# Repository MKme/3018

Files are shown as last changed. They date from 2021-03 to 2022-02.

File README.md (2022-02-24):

<p align="center">
<b>Adventures with the 3018 CNC Router </b><br>
<br><br>
<br>🐦 <a href="https://twitter.com/mkmeorg">Twitter</a>
| 📺 <a href="https://www.youtube.com/mkmeorg">YouTube</a>
| 🌍 <a href="http://www.mkme.org">mkme.org</a><br>
<br>
Support this project and become a patron on <a href="https://www.patreon.com/EricWilliam">Patreon</a>.<br>
Chat: <a href="https://discord.gg/j9S4Fgv">Discord</a></b>!
</p>

# 3018
I bought the 3018 CNC as a cheap DIY kit and built it live on YouTube at the links below.  This repo is where I am storing all the information, guides, tutorials, parts and supplies  use in this build.
I have linked the exact parts and supplies you will see in upcoming videos on the main channel. So far it seems to be a great kit.  I am totally new to CNC but have 3D Printing and laser cutting experience. 

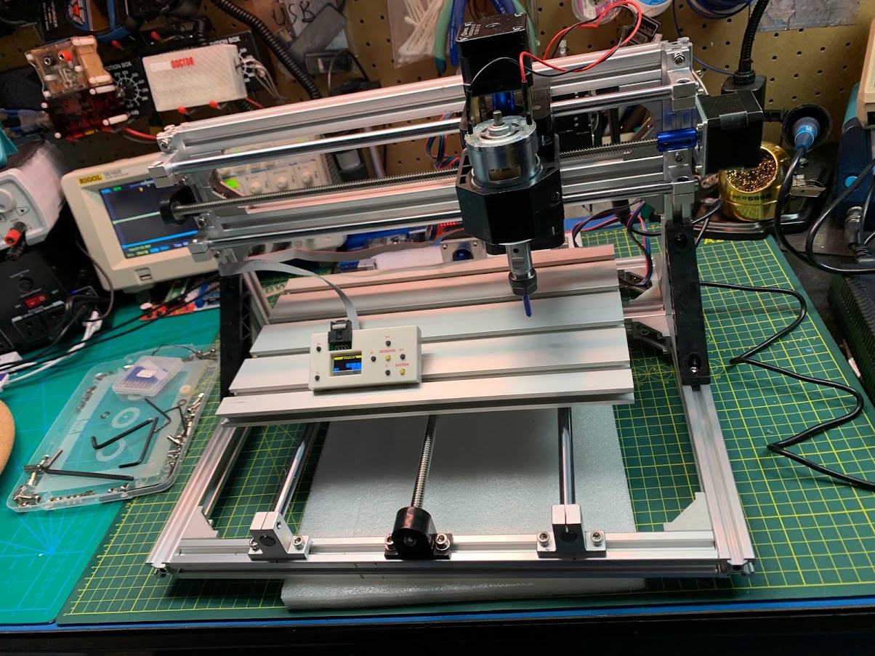
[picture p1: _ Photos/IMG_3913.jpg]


## Parts:

All the parts Ive used to build the 3018 and upgrades I have added 

| Component | Source  |
| --- |---|
| Amazon- 3018 CNC Machine | https://amzn.to/3pK1ZLT
| Ebay- Router Kit CNC 3018 Pro Machine 3 Axis 10000 rpm Mill PCB Engraver GRBL Control| https://ebay.us/W8HP4r
| Offline GRBL Controller| https://ebay.us/ckhK1e
| ER11 Collet Set | https://amzn.to/343iBWA
| End Mill, 10pcs Tungsten Carbide End Mill Single Flute Spiral CNC Router Bits 1/8 inch Shank 3.175x17mm for Cutting Acrylic, PVC, MDF, Density Board, Wood and Many Other Soft Materials | https://amzn.to/3FMRVaG
| Spoilboard | https://amzn.to/3pHBZRw
| 1" / 1/4" Spoilboard facing bit| https://amzn.to/3sNfIDH
| Spiral Wire Wrap | https://amzn.to/3FH86WW
| Clear Enclosure box for CNC | https://amzn.to/3eEoEmz 
| 5Pcs HSS CNC Straight Shank 4 Flute End Mill Cutter Drill Bit Tool 4/6/8/10/12mm  | https://ebay.us/2YhFQY
| 3.175mm Shank Carbide Ball Nose End Mill CNC Engraving Router bit Set 1-3.175mm | https://ebay.us/iut9AZ
| Router Z-CheckPlate Setting Probe | https://ebay.us/5xJLyh
| 10Pc 20 Degree 0.1mm Carbide PCB Engraving Bits CNC Router Tool 3.175mm Shank | https://ebay.us/X4Ojiy
| 10 X 1/8 Shank Titanium Coated End Mill Carbide CNC Milling Cutter Router Bits | https://ebay.us/idcgTA
| 10pcs 3.175mm Titanium Coated PCB Carbide Milling Cutter CNC Router Bit 1.0mm | https://ebay.us/ZVp0hr
| Air Pressure Regulator with water trap | https://ebay.us/2Yts93
| Air Pressure Regulator (no trap) | https://ebay.us/ZeRWfh

Handy Supplies 

| Component | Source  |
| --- |---|
| FR4 Copper Blanks | https://amzn.to/34dta9L
| 150mm Vernier Caliper Stainless Steel Digital Caliper 6 inch | https://ebay.us/4c7PpS
| Drill Size Gauge 29 Holes 1/16 to 1/2" Sizes Bolt Wire Diameter Index Sizer| https://ebay.us/jrOKvM

## Forum Thread 

Forum thread of my build: https://forum.mkme.org/viewtopic.php?f=5&p=1539#p1539

## Full videos here:

### I assembled the entire 3018 CNC kit live on MKME.tv YouTube channel

Full Playlist:  https://www.youtube.com/playlist?list=PLf_FeOPE7t5oFH7cH6LmOSjlNVdHZGadV

Part 1: https://www.youtube.com/watch?v=dMigu1GxnhI

Part 2: https://www.youtube.com/watch?v=k8vIYXJhONk

Part 3: https://www.youtube.com/watch?v=uXbvilvltno

Part 4: https://www.youtube.com/watch?v=I1g_5FwFcC8

Part 5: https://www.youtube.com/watch?v=GIUuVpB_j9A 

### NOOBs Guide To First Cuts 

1.  CAM software is needed to generate the GCODE - Fusion 360 is what I have already in use for 3D Printing 
2. Connect Candle to the CNC and type $$ in to console- save this output as a backup file for initial config 

### Guidlines and definitions from Facebook group docs (not mine) 

$0=10 Step pulse, microseconds 3-15 ish (only the 15 is ish)

$1=25 Step idle delay, milliseconds 15-30 ish OR 255

$2=0 Step port invert, mask Only 0-7

$3=2 Direction port invert, mask Only 0-7

$4=0 Step enable invert, boolean Only 0 or 1

$5=0 Limit pins invert, boolean Only 0 or 1

$6=0 Probe pin invert, boolean Only 0 or 1

$10=1 Status report, mask Only 0-3

$11=0.010 Junction deviation, mm 0.1 to 0.001 ish

$12=0.002 Arc tolerance, mm 0.1 to 0.001 ish

$13=0 Report inches, boolean Only 0 or 1

$20=0 Soft limits, boolean Only 0 or 1

$21=0 Hard limits, boolean Only 0 or 1

$22=0 Homing cycle, boolean Only 0 or 1

$23=0 Homing dir invert, mask Only 0-7

$24=25.000 Homing feed, mm/min 10-50 ish

$25=500.000 Homing seek, mm/min 250-750 ish

$26=250 Homing debounce, milliseconds 5-50 ish Yes I know my default setting is wrong but it is not used.

$27=1.000 Homing pull-off, mm 0.5-3.5 ish

$30=1000 Max spindle speed, RPM 750-7500 ish

$31=0 Min spindle speed, RPM 0-100 ish

$32=0 Laser mode, boolean 0 or 1 1 ONLY when using a laser

$100=800.000 X steps/mm 800 or 1600*

$101=800.000 Y steps/mm 800 or 1600*

$102=800.000 Z steps/mm 800 or 1600*

$110=1000.000 X Max rate, mm/min 500-2000 ish

$111=1000.000 Y Max rate, mm/min 500-2000 ish

$112=600.000 Z Max rate, mm/min 500-2000 ish

$120=30.000 X Acceleration, mm/sec^2 20-10000 ish

$121=30.000 Y Acceleration, mm/sec^2 20-10000 ish

$122=30.000 Z Acceleration, mm/sec^2 20-10000 ish

$130=200.000 X Max travel, mm Around your router size ish

$131=200.000 Y Max travel, mm Around your router size ish

$132=200.000 Z Max travel, mm Around your router size ish

*
These values ($100-102) should all be the same. If only 2 are the same set the third accordingly. Other values are possible 
but 800 or 1600 are overwhelmingly common for this sort of router. However the tests you are going to run check these 
settings.

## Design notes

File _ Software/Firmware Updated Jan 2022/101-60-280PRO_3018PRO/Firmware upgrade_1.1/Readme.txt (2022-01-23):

1. If you need to upgrade the firmware to version 1.1, you can use the USB cable to connect to the motherboard and power it on.

2. Please check the 'manual' from the folder 'XLoader&GRBL1.1F-CNC3'to upgrade.

3. Then you can use the control software 'Grblcontrol(Candle_1.1.7 )' to control the CNC Router.

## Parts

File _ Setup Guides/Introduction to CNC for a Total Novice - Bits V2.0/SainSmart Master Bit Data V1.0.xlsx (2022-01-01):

SAINSMART Bits and End Mills |  |  | By Graham Bland Nov 2020 |  | V1.0 |  |  |  | Fusion 360 Millng Bits and Drill |  |  |  |  |  |  |  |  |  |  |  |  |  |  |  |  |  |  |  |  |  |  | Vcarve Bits
Holder: | ER11-A |  |  |  |  |  |  |  | Type | Clockwise | Number of Flutes | Material | Dia | Shaft Dia | OA Length | Length below Holder | Shoulder length | Flute Length | Corner Radius | Taper Angle (One side) | Tip Length | Tip Dia | Tip Angle | Thread Pitch | Number of Teeth | Thread Profile Angle | Shaft Height | Shaft Upper Dia | Shaft Lower Dia |  | NOTE: The tool name in V-Carve is derived from a number of parameter values. In the tool library some of these have been edited to either differentiate between similar bits or provide more information than is present in the tool parameters. | Type | Diameter | Flutes | Tip Radius | Included Angle | Side Angle | Flat Diameter | Tooth Height | Tooth Size | Tooth Offset | Neck Length
SainSmart ER11 Spring Collet Set 1.0mm-7.0mm |  |  |  |  | Clamping Length mm | 18 |  |  | ball end mill | X | X | X | X | X | X | X | X | X |  |  |  |  |  |  |  |  | Shaft starts above the shoulder length of a bit and is used to describe any contours on the shaft before it reaches the Shaft Dia. Normally not needed and is only used for collision detection (I think) Shaft segments start at the top Index 1 being the highest. |  |  |  |  | Ball Nose | X | X
Collets for ER11 | Internal Dia |  |  |  |  |  |  |  | bull nose end mill | X | X | X | X | X | X | X | X | X | X |  |  |  |  |  |  |  |  |  |  |  |  | End Mill | X | X
 | 1mm |  |  |  |  |  |  |  | chamfer mill | X | X | X | X | X | X | X | X | X |  | X |  | X |  |  |  |  |  |  |  |  |  | Radiused End Mill | X | X | X
 | 2mm |  |  |  |  |  |  |  | dovetail mill | X | X | X | X | X | X | X | X | X | X | X |  |  |  |  |  |  |  |  |  |  |  | V-Bit | X | X |  | X
 | 3mm |  |  |  |  |  |  |  | face mill | X | X | X | X | X | X | X | X | X | X | X |  |  |  |  |  |  |  |  |  |  |  | Engraving | X | X |  |  | X | X
 | 4mm |  |  |  |  |  |  |  | flat end mill | X | X | X | X | X | X | X | X | X |  |  |  |  |  |  |  |  |  |  |  |  |  | Tapered Ball Nose | X | X | X |  | X
 | 5mm |  |  |  |  |  |  |  | lollipop mill | X | X | X | X | X | X | X | X | X |  |  |  |  |  |  |  |  |  |  |  |  |  | Drill | X | X |  | X
 | 6mm |  |  |  |  |  |  |  | radius mill | X | X | X | X | X | X | X | X | X | X |  | X |  |  |  |  |  |  |  |  |  |  | Thread Mill | X | X |  | X |  |  | X | X | X | X
 | 7mm |  |  |  |  |  |  |  | slot mill | X | X | X | X | X | X | X | X | X | X |  |  |  |  |  |  |  |  |  |  |  |  | Form Tool
NOTES: |  |  |  |  |  |  |  |  | tapered mill/Ball | X | X | X | X | X | X | X | X | X | X | X |  |  |  |  |  |  |  |  |  |  |  | Diamond Drag | X |  |  | X
The collet which came with your machine is almost certainly a 3mm or 1/8" (3.175mm) These collets will take a bit with a shaft diameter of 3 or 3.175mm If you are intending to use bits with a larger or smaller shaft diameter you will need a suitable collet. |  |  |  |  |  |  |  |  | tapered mill/Bull Nose | X | X | X | X | X | X | X | X | X | X | X
 |  |  |  |  |  |  |  |  | thread mill | X | X | X | X | X | X | X | X | X |  |  |  |  |  | X | X | X
The bits are sold individually or in sets. As this is just defining the bits any multiple identical bits in the same set are only defined once. |  |  |  |  |  |  |  |  | form mill | X | X | X | X | X | X | X |  | X
Fusion 360 has the most comprehensive description of a bit I have found, any other software has their values based on these using simple formulas. There are some exceptions to the simple rules, any overrides will be either in red or italics |  |  |  |  |  |  |  |  | Drill | X | X | X | X | X | X | X | X | X |  |  |  |  | X
 |  |  |  |  |  |  |  |  | Fusion 360 Setup |  |  |  |  |  |  |  |  |  |  |  |  |  |  |  |  |  |  |  |  | Vcarve Setup
Pack Description | Website Ref | Pack Qty | Same Varied | Bit Material | SKU | Coating | Individual Description | Product ID | Type | Clockwise | Number of Flutes | Material | Dia | Shaft Dia | OA Length | Length below Holder | Shoulder length | Flute Length | Corner Radius | Taper Angle (One side) | Tip Length | Tip Dia | Tip Angle | Thread Pitch | Number of Teeth | Thread Profile Angle | Shaft Height | Shaft Upper Dia | Shaft Lower Dia | Group Name | Notes | Type | Diameter | Flutes | Tip Radius | Included Angle | Side Angle | Flat Diameter | Tooth Height | Tooth Size | Tooth Offset | Neck Length
Genmitsu 1/8" Engraving Bits 10-PCS 20 Degree Set V20, 0.1mm, Nano Blue Coating | V20 | 10 | Same | Tungsten Carbide Steel Alloy | 101-60-70V20 | Nano Blue Coat | V Engraving Bit 20 Deg 0.1mm Tip | V20 | chamfer mill | yes | 1 | Ti Coated | 3.175 | 3.175 | 27 | 17 | 15 | 14 |  | 10 |  | 0.1 |  |  |  |  |  |  |  | SainSmart [V20] V Engraving 20 Deg | SainSmart [V20] V Engraving Bit 20 Deg 0.1mm Tip Nano Blue Coat | Engraving | 3.175 | 1 |  |  | 10 | 0.1
 | Images
 |  |  |  |  |  |  |  |  | Fusion 360 Setup |  |  |  |  |  |  |  |  |  |  |  |  |  |  |  |  |  |  |  |  | Vcarve Setup
Pack Description | Website Ref | Pack Qty | Same Varied | Bit Material | SKU | Coating | Individual Description | Product ID | Type | Clockwise | Number of Flutes | Material | Dia | Shaft Dia | OA Length | Length below Holder | Shoulder length | Flute Length | Corner Radius | Taper Angle (One side) | Tip Length | Tip Dia | Tip Angle | Thread Pitch | Number of Teeth | Thread Profile Angle | Shaft Height | Shaft Upper Dia | Shaft Lower Dia | Group Name | Notes | Type | Diameter | Flutes | Tip Radius | Included Angle | Side Angle | Flat Diameter | Tooth Height | Tooth Size | Tooth Offset | Neck Length
Genmitsu 1/8" Engraving Bits 10-PCS 15 Degree Set V15, 0.1mm, Nano Blue Coating | V15 | 10 | Same | Tungsten Carbide Steel Alloy | 101-60-70V15 | Nano Blue Coat | V Engraving Bit 15 Deg 0.1mm Tip | V15 | chamfer mill | yes | 1 | Ti Coated | 3.175 | 3.175 | 29 | 17 | 16 | 15 |  | 7.5 |  | 0.1 |  |  |  |  |  |  |  | SainSmart [V15] V Engraving 15 Deg | SainSmart [V15] V Engraving Bit 15 Deg 0.1mm Tip Nano Blue Coat | Engraving | 3.175 | 1 |  |  | 7.5 | 0.1
 | Images
 |  |  |  |  |  |  |  |  | Fusion 360 Setup |  |  |  |  |  |  |  |  |  |  |  |  |  |  |  |  |  |  |  |  | Vcarve Setup
Pack Description | Website Ref | Pack Qty | Same Varied | Bit Material | SKU | Coating | Individual Description | Product ID | Type | Clockwise | Number of Flutes | Material | Dia | Shaft Dia | OA Length | Length below Holder | Shoulder length | Flute Length | Corner Radius | Taper Angle (One side) | Tip Length | Tip Dia | Tip Angle | Thread Pitch | Number of Teeth | Thread Profile Angle | Shaft Height | Shaft Upper Dia | Shaft Lower Dia | Group Name | Notes | Type | Diameter | Flutes | Tip Radius | Included Angle | Side Angle | Flat Diameter | Tooth Height | Tooth Size | Tooth Offset | Neck Length
Genmitsu 1/8" Engraving Bits 10-PCS 30 Degree Set V30, 0.1mm, Nano Blue Coating | V30 | 10 | Same | Tungsten Carbide Steel Alloy | 101-60-70V30 | Nano Blue Coat | V Engraving Bit 30 Deg 0.1mm Tip | V30 | chamfer mill | yes | 1 | Ti Coated | 3.175 | 3.175 | 27 | 17 | 16 | 15 |  | 15 |  | 0.1 |  |  |  |  |  |  |  | SainSmart [V30] V Engraving 30 Deg | SainSmart [V30] V Engraving Bit 30 Deg 0.1mm Tip Nano Blue Coat | Engraving | 3.175 | 1 |  |  | 15 | 0.1
 | Images
 |  |  |  |  |  |  |  |  | Fusion 360 Setup |  |  |  |  |  |  |  |  |  |  |  |  |  |  |  |  |  |  |  |  | Vcarve Setup
Pack Description | Website Ref | Pack Qty | Same Varied | Bit Material | SKU | Coating | Individual Description | Product ID | Type | Clockwise | Number of Flutes | Material | Dia | Shaft Dia | OA Length | Length below Holder | Shoulder length | Flute Length | Corner Radius | Taper Angle (One side) | Tip Length | Tip Dia | Tip Angle | Thread Pitch | Number of Teeth | Thread Profile Angle | Shaft Height | Shaft Upper Dia | Shaft Lower Dia | Group Name | Notes | Type | Diameter | Flutes | Tip Radius | Included Angle | Side Angle | Flat Diameter | Tooth Height | Tooth Size | Tooth Offset | Neck Length
Genmitsu 1/8" Router Bit 10-PCS Variety Set C08, 0.8-3.0mm Nano Blue Coating | C08 | 10 | Same (Dia) | Tungsten Carbide Steel Alloy | 101-60-70C08 | Nano Blue Coat | Router Corncob 2 Flute | C08 | flat end mill | yes | 2 | Ti Coated | 0.8 | 3.175 | 37 | 19 | 7 | 6 |  |  |  |  |  |  |  |  | 7 | 3.175 | 0.8 | SainSmart [C08] Router 0.8-3.0mm | SainSmart [C08] Router Corncob 2 Flute Nano Blue Coat | End Mill | 0.8 | 2
 | Images |  |  |  |  |  | Router Corncob 2 Flute | C08 | flat end mill | yes | 2 | Ti Coated | 1 | 3.175 | 37 | 19 | 9 | 6 |  |  |  |  |  |  |  |  | 5 | 3.175 | 1 |  | SainSmart [C08] Router Corncob 2 Flute Nano Blue Coat | End Mill | 1 | 2
 |  |  |  |  |  |  | Router Corncob 2 Flute | C08 | flat end mill | yes | 2 | Ti Coated | 1.2 | 3.175 | 37 | 19 | 9 | 7 |  |  |  |  |  |  |  |  | 5 | 3.175 | 1.2 |  | SainSmart [C08] Router Corncob 2 Flute Nano Blue Coat | End Mill | 1.2 | 2
 |  |  |  |  |  |  | Router Corncob 2 Flute | C08 | flat end mill | yes | 2 | Ti Coated | 1.4 | 3.175 | 37 | 19 | 9 | 8 |  |  |  |  |  |  |  |  | 5 | 3.175 | 1.4 |  | SainSmart [C08] Router Corncob 2 Flute Nano Blue Coat | End Mill | 1.4 | 2
 |  |  |  |  |  |  | Router Corncob 2 Flute | C08 | flat end mill | yes | 2 | Ti Coated | 1.6 | 3.175 | 37 | 19 | 10 | 8 |  |  |  |  |  |  |  |  | 4 | 3.175 | 1.6 |  | SainSmart [C08] Router Corncob 2 Flute Nano Blue Coat | End Mill | 1.6 | 2
 |  |  |  |  |  |  | Router Corncob 2 Flute | C08 | flat end mill | yes | 2 | Ti Coated | 1.8 | 3.175 | 37 | 19 | 10 | 8 |  |  |  |  |  |  |  |  | 4 | 3.175 | 1.8 |  | SainSmart [C08] Router Corncob 2 Flute Nano Blue Coat | End Mill | 1.8 | 2
 |  |  |  |  |  |  | Router Corncob 2 Flute | C08 | flat end mill | yes | 2 | Ti Coated | 2 | 3.175 | 37 | 19 | 10 | 8 |  |  |  |  |  |  |  |  | 4 | 3.175 | 2 |  | SainSmart [C08] Router Corncob 2 Flute Nano Blue Coat | End Mill | 2 | 2
 |  |  |  |  |  |  | Router Corncob 2 Flute | C08 | flat end mill | yes | 2 | Ti Coated | 2.2 | 3.175 | 37 | 19 | 10 | 8 |  |  |  |  |  |  |  |  | 4 | 3.175 | 2.2 |  | SainSmart [C08] Router Corncob 2 Flute Nano Blue Coat | End Mill | 2.2 | 2
 |  |  |  |  |  |  | Router Corncob 2 Flute | C08 | flat end mill | yes | 2 | Ti Coated | 2.4 | 3.175 | 37 | 19 | 10 | 8 |  |  |  |  |  |  |  |  | 4 | 3.175 | 2.4 |  | SainSmart [C08] Router Corncob 2 Flute Nano Blue Coat | End Mill | 2.4 | 2
 |  |  |  |  |  |  | Router Corncob 2 Flute | C08 | flat end mill | yes | 2 | Ti Coated | 3 | 3.175 | 37 | 19 | 12 | 10 |  |  |  |  |  |  |  |  | 2 | 3.175 | 3 |  | SainSmart [C08] Router Corncob 2 Flute Nano Blue Coat | End Mill | 3 | 2
 |  |  |  |  |  |  |  |  | Fusion 360 Setup |  |  |  |  |  |  |  |  |  |  |  |  |  |  |  |  |  |  |  |  | Vcarve Setup
Pack Description | Website Ref | Pack Qty | Same Varied | Bit Material | SKU | Coating | Individual Description | Product ID | Type | Clockwise | Number of Flutes | Material | Dia | Shaft Dia | OA Length | Length below Holder | Shoulder length | Flute Length | Corner Radius | Taper Angle (One side) | Tip Length | Tip Dia | Tip Angle | Thread Pitch | Number of Teeth | Thread Profile Angle | Shaft Height | Shaft Upper Dia | Shaft Lower Dia | Group Name | Notes | Type | Diameter | Flutes | Tip Radius | Included Angle | Side Angle | Flat Diameter | Tooth Height | Tooth Size | Tooth Offset | Neck Length
Genmitsu 1/8" Router Bit 10-PCS Variety Set C15, 1.5-3.175mm Nano Blue Coating | C15 | 10 | Same (Dia) | Tungsten Carbide Steel Alloy | 101-60-70C15 | Nano Blue Coat | Router Corncob 2 Flute | C15 | flat end mill | yes | 2 | Ti Coated | 1.5 | 3.175 | 37 | 19 | 10 | 8 |  |  |  |  |  |  |  |  | 4 | 3.175 | 1.5 | SainSmart [C15] Router 1.5-3.175mm | SainSmart [C15] Router Corncob 2 Flute Nano Blue Coat | End Mill | 1.5 | 2
 | Images |  |  |  |  |  | Router Corncob 2 Flute | C15 | flat end mill | yes | 2 | Ti Coated | 1.6 | 3.175 | 37 | 19 | 10 | 8 |  |  |  |  |  |  |  |  | 4 | 3.175 | 1.6 |  | SainSmart [C15] Router Corncob 2 Flute Nano Blue Coat | End Mill | 1.6 | 2
 |  |  |  |  |  |  | Router Corncob 2 Flute | C15 | flat end mill | yes | 2 | Ti Coated | 1.7 | 3.175 | 37 | 19 | 10 | 8 |  |  |  |  |  |  |  |  | 4 | 3.175 | 1.7 |  | SainSmart [C15] Router Corncob 2 Flute Nano Blue Coat | End Mill | 1.7 | 2
 |  |  |  |  |  |  | Router Corncob 2 Flute | C15 | flat end mill | yes | 2 | Ti Coated | 1.8 | 3.175 | 37 | 19 | 10 | 8 |  |  |  |  |  |  |  |  | 4 | 3.175 | 1.8 |  | SainSmart [C15] Router Corncob 2 Flute Nano Blue Coat | End Mill | 1.8 | 2
 |  |  |  |  |  |  | Router Corncob 2 Flute | C15 | flat end mill | yes | 2 | Ti Coated | 2 | 3.175 | 37 | 19 | 10 | 8 |  |  |  |  |  |  |  |  | 4 | 3.175 | 2 |  | SainSmart [C15] Router Corncob 2 Flute Nano Blue Coat | End Mill | 2 | 2
 |  |  |  |  |  |  | Router Corncob 2 Flute | C15 | flat end mill | yes | 2 | Ti Coated | 2.2 | 3.175 | 37 | 19 | 10 | 8 |  |  |  |  |  |  |  |  | 4 | 3.175 | 2.2 |  | SainSmart [C15] Router Corncob 2 Flute Nano Blue Coat | End Mill | 2.2 | 2
 |  |  |  |  |  |  | Router Corncob 2 Flute | C15 | flat end mill | yes | 2 | Ti Coated | 2.4 | 3.175 | 37 | 19 | 10 | 8 |  |  |  |  |  |  |  |  | 4 | 3.175 | 2.4 |  | SainSmart [C15] Router Corncob 2 Flute Nano Blue Coat | End Mill | 2.4 | 2
 |  |  |  |  |  |  | Router Corncob 2 Flute | C15 | flat end mill | yes | 2 | Ti Coated | 2.5 | 3.175 | 37 | 19 | 10 | 8 |  |  |  |  |  |  |  |  | 4 | 3.175 | 2.5 |  | SainSmart [C15] Router Corncob 2 Flute Nano Blue Coat | End Mill | 2.5 | 2
 |  |  |  |  |  |  | Router Corncob 2 Flute | C15 | flat end mill | yes | 2 | Ti Coated | 3 | 3.175 | 37 | 19 | 11 | 9 |  |  |  |  |  |  |  |  | 2 | 3.175 | 3 |  | SainSmart [C15] Router Corncob 2 Flute Nano Blue Coat | End Mill | 3 | 2
 |  |  |  |  |  |  | Router Corncob 2 Flute | C15 | flat end mill | yes | 2 | Ti Coated | 3.175 | 3.175 | 37 | 19 | 12 | 10 |  |  |  |  |  |  |  |  |  |  |  |  | SainSmart [C15] Router Corncob 2 Flute Nano Blue Coat | End Mill | 3.175 | 2
 |  |  |  |  |  |  |  |  | Fusion 360 Setup |  |  |  |  |  |  |  |  |  |  |  |  |  |  |  |  |  |  |  |  | Vcarve Setup
Pack Description | Website Ref | Pack Qty | Same Varied | Bit Material | SKU | Coating | Individual Description | Product ID | Type | Clockwise | Number of Flutes | Material | Dia | Shaft Dia | OA Length | Length below Holder | Shoulder length | Flute Length | Corner Radius | Taper Angle (One side) | Tip Length | Tip Dia | Tip Angle | Thread Pitch | Number of Teeth | Thread Profile Angle | Shaft Height | Shaft Upper Dia | Shaft Lower Dia | Group Name | Notes | Type | Diameter | Flutes | Tip Radius | Included Angle | Side Angle | Flat Diameter | Tooth Height | Tooth Size | Tooth Offset | Neck Length
Genmitsu 1/8" Router Bit 10-PCS Ball Nose Set SB17, Nano Blue Coating | SB17 | 10 | Same | Tungsten Carbide Steel Alloy | 101-60-70SB17 | Nano Blue Coat | Ball Nose 2 Flute | SB17 | ball end mill | yes | 2 | Ti Coated | 3.175 | 3.175 | 38 | 23 | 22 | 17 |  |  |  |  |  |  |  |  |  |  |  | SainSmart [SB17] Ball Nose 2 Flute | SainSmart [SB17] Ball Nose 2 Flute Nano Blue Coat | Ball Nose | 3.175 | 2
 | Images
 |  |  |  |  |  |  |  |  | Fusion 360 Setup |  |  |  |  |  |  |  |  |  |  |  |  |  |  |  |  |  |  |  |  | Vcarve Setup
Pack Description | Website Ref | Pack Qty | Same Varied | Bit Material | SKU | Coating | Individual Description | Product ID | Type | Clockwise | Number of Flutes | Material | Dia | Shaft Dia | OA Length | Length below Holder | Shoulder length | Flute Length | Corner Radius | Taper Angle (One side) | Tip Length | Tip Dia | Tip Angle | Thread Pitch | Number of Teeth | Thread Profile Angle | Shaft Height | Shaft Upper Dia | Shaft Lower Dia | Group Name | Notes | Type | Diameter | Flutes | Tip Radius | Included Angle | Side Angle | Flat Diameter | Tooth Height | Tooth Size | Tooth Offset | Neck Length
Genmitsu 1/8" Router Bit 10-PCS Flat Nose Set SS17, 1 Flute, Nano Blue Coating | SS17 | 10 | Same | Tungsten Carbide Steel Alloy | 101-60-70SS17 | Nano Blue Coat | Flat Nose 1 Flute | SS17 | flat end mill | yes | 1 | Ti Coated | 3.175 | 3.175 | 38 | 20 | 18 | 17 |  |  |  |  |  |  |  |  |  |  |  | SainSmart [SS17] Flat Nose 1 Flute | SainSmart [SS17] Flat Nose 1 Flute Nano Blue Coat | End Mill | 3.175 | 1
 | Images
 |  |  |  |  |  |  |  |  | Fusion 360 Setup |  |  |  |  |  |  |  |  |  |  |  |  |  |  |  |  |  |  |  |  | Vcarve Setup
Pack Description | Website Ref | Pack Qty | Same Varied | Bit Material | SKU | Coating | Individual Description | Product ID | Type | Clockwise | Number of Flutes | Material | Dia | Shaft Dia | OA Length | Length below Holder | Shoulder length | Flute Length | Corner Radius | Taper Angle (One side) | Tip Length | Tip Dia | Tip Angle | Thread Pitch | Number of Teeth | Thread Profile Angle | Shaft Height | Shaft Upper Dia | Shaft Lower Dia | Group Name | Notes | Type | Diameter | Flutes | Tip Radius | Included Angle | Side Angle | Flat Diameter | Tooth Height | Tooth Size | Tooth Offset | Neck Length
Genmitsu 1/8" Router Bit 10-PCS Flat Nose Set SF17, 2 Flute, Nano Blue Coating | SF17 | 10 | Same | Tungsten Carbide Steel Alloy | 101-60-70SF17 | Nano Blue Coat | Flat Nose 2 Flute | SF17 | flat end mill | yes | 2 | Ti Coated | 3.175 | 3.175 | 38 | 22 | 22 | 16 |  |  |  |  |  |  |  |  |  |  |  | SainSmart [SF17] Flat Nose 2 Flute | SainSmart [SF17] Flat Nose 2 Flute Nano Blue Coat | End Mill | 3.175 | 2
 | Images
 |  |  |  |  |  |  |  |  | Fusion 360 Setup |  |  |  |  |  |  |  |  |  |  |  |  |  |  |  |  |  |  |  |  | Vcarve Setup
Pack Description | Website Ref | Pack Qty | Same Varied | Bit Material | SKU | Coating | Individual Description | Product ID | Type | Clockwise | Number of Flutes | Material | Dia | Shaft Dia | OA Length | Length below Holder | Shoulder length | Flute Length | Corner Radius | Taper Angle (One side) | Tip Length | Tip Dia | Tip Angle | Thread Pitch | Number of Teeth | Thread Profile Angle | Shaft Height | Shaft Upper Dia | Shaft Lower Dia | Group Name | Notes | Type | Diameter | Flutes | Tip Radius | Included Angle | Side Angle | Flat Diameter | Tooth Height | Tooth Size | Tooth Offset | Neck Length
Genmitsu Diamond Dresser Pen | DM-1350 | 1 | Single | Tungsten Carbide Steel Alloy | 101-60-DMB-01 |  | Diamond Dresser Pen 50Deg | DM-1350 | chamfer mill | yes | 1 |  | 3.175 | 3.175 | 50 | 32 | 2.5 | 0.75 |  | 25 |  | 0 |  |  |  |  |  |  |  | SainSmart [DM-1350] Diamond Dresser | SainSmart [DM-1350] Diamond Dresser Pen 50Deg | Diamond Drag | 3.175 |  |  | 50
 | Images
 |  |  |  |  |  |  |  |  | Fusion 360 Setup |  |  |  |  |  |  |  |  |  |  |  |  |  |  |  |  |  |  |  |  | Vcarve Setup
Pack Description | Website Ref | Pack Qty | Same Varied | Bit Material | SKU | Coating | Individual Description | Product ID | Type | Clockwise | Number of Flutes | Material | Dia | Shaft Dia | OA Length | Length below Holder | Shoulder length | Flute Length | Corner Radius | Taper Angle (One side) | Tip Length | Tip Dia | Tip Angle | Thread Pitch | Number of Teeth | Thread Profile Angle | Shaft Height | Shaft Upper Dia | Shaft Lower Dia | Group Name | Notes | Type | Diameter | Flutes | Tip Radius | Included Angle | Side Angle | Flat Diameter | Tooth Height | Tooth Size | Tooth Offset | Neck Length
Square End Mill, 1.0-6.0mm cut diameter, 4-Flute |  | N/A | Single | Tungsten Carbide Steel Alloy | 101-60-NBS-0(1-9) | Nano Blue Coat | Square 4 Flute | S-400010450 | flat end mill | yes | 4 | Ti Coated | 1 | 4 | 50 | 32 | 5 | 3 |  |  |  |  |  |  |  |  | 8 | 4 | 1 | SainSmart [101-60-NBS-0x] Square End 4 Flute | SainSmart [S-400010450] Square 4 Flute Nano Blue Coat | End Mill | 1 | 4
 | Images |  |  |  |  |  | Square 4 Flute | S-400015450 | flat end mill | yes | 4 | Ti Coated | 1.5 | 4 | 50 | 32 | 5.5 | 4 |  |  |  |  |  |  |  |  | 6 | 4 | 1.5 |  | SainSmart [S-400015450] Square 4 Flute Nano Blue Coat | End Mill | 1.5 | 4
 |  |  |  |  |  |  | Square 4 Flute | S-400020450 | flat end mill | yes | 4 | Ti Coated | 2 | 4 | 50 | 32 | 6.5 | 5 |  |  |  |  |  |  |  |  | 6 | 4 | 2 |  | SainSmart [S-400020450] Square 4 Flute Nano Blue Coat | End Mill | 2 | 4
 |  |  |  |  |  |  | Square 4 Flute | S-400025450 | flat end mill | yes | 4 | Ti Coated | 2.5 | 4 | 50 | 32 | 8.25 | 6.25 |  |  |  |  |  |  |  |  | 5 | 4 | 2.5 |  | SainSmart [S-400025450] Square 4 Flute Nano Blue Coat | End Mill | 2.5 | 4
 |  |  |  |  |  |  | Square 4 Flute | S-400030450 | flat end mill | yes | 4 | Ti Coated | 3 | 4 | 50 | 32 | 9.5 | 7.5 |  |  |  |  |  |  |  |  | 3.5 | 4 | 3 |  | SainSmart [S-400030450] Square 4 Flute Nano Blue Coat | End Mill | 3 | 4
 |  |  |  |  |  |  | Square 4 Flute | S-400035450 | flat end mill | yes | 4 | Ti Coated | 3.5 | 4 | 50 | 32 | 12 | 10 |  |  |  |  |  |  |  |  | 3 | 4 | 3.5 |  | SainSmart [S-400035450] Square 4 Flute Nano Blue Coat | End Mill | 3.5 | 4
 |  |  |  |  |  |  | Square 4 Flute | S-400040450 | flat end mill | yes | 4 | Ti Coated | 4 | 4 | 50 | 32 | 12 | 10 |  |  |  |  |  |  |  |  |  |  |  |  | SainSmart [S-400040450] Square 4 Flute Nano Blue Coat | End Mill | 4 | 4
 |  |  |  |  |  |  | Square 4 Flute | S-400050650 | flat end mill | yes | 4 | Ti Coated | 5 | 6 | 50 | 32 | 15 | 12.5 |  |  |  |  |  |  |  |  | 3 | 6 | 5 |  | SainSmart [S-400050650] Square 4 Flute Nano Blue Coat | End Mill | 5 | 4
 |  |  |  |  |  |  | Square 4 Flute | S-400060650 | flat end mill | yes | 4 | Ti Coated | 6 | 6 | 50 | 32 | 16 | 15 |  |  |  |  |  |  |  |  |  |  |  |  | SainSmart [S-400060650] Square 4 Flute Nano Blue Coat | End Mill | 6 | 4
NOTE: The following bits are sold individually or in sets for a purpose. As this is just defining the bits the actual packs have been ignored |  |  |  |  |  |  |  |  | Fusion 360 Setup |  |  |  |  |  |  |  |  |  |  |  |  |  |  |  |  |  |  |  |  | Vcarve Setup
Pack Description | Website Ref | Pack Qty | Same Varied | Bit Material | SKU | Coating | Individual Description | Product ID | Type | Clockwise | Number of Flutes | Material | Dia | Shaft Dia | OA Length | Length below Holder | Shoulder length | Flute Length | Corner Radius | Taper Angle (One side) | Tip Length | Tip Dia | Tip Angle | Thread Pitch | Number of Teeth | Thread Profile Angle | Shaft Height | Shaft Upper Dia | Shaft Lower Dia | Group Name | Notes | Type | Diameter | Flutes | Tip Radius | Included Angle | Side Angle | Flat Diameter | Tooth Height | Tooth Size | Tooth Offset | Neck Length
Genmitsu CNC Ball Nose End Mill |  | N/A | Single | Tungsten Carbide Steel Alloy | 101-60-NBB-0(1-6) | Nano Blue Coat | Ball Nose 2 Flute | B-210020450 | ball end mill | yes | 2 | Ti Coated | 2 | 4 | 50 | 32 | 6 | 4 |  |  |  |  |  |  |  |  | 4.5 | 4 | 2 | SainSmart [101-60-NBB-0x] Ball Nose 2 Flute | SainSmart [B-210020450] Ball Nose 2 Flute Nano Blue Coat | Ball Nose | 2 | 2
 | Images |  |  |  |  |  | Ball Nose 2 Flute | B-212525450 | ball end mill | yes | 2 | Ti Coated | 2.5 | 4 | 50 | 32 | 7 | 5 |  |  |  |  |  |  |  |  | 4.5 | 4 | 2.5 |  | SainSmart [B-212525450] Ball Nose 2 Flute Nano Blue Coat | Ball Nose | 2.5 | 2
 |  |  |  |  |  |  | Ball Nose 2 Flute | B-215030450 | ball end mill | yes | 2 | Ti Coated | 3 | 4 | 50 | 32 | 8 | 6 |  |  |  |  |  |  |  |  | 3 | 4 | 3 |  | SainSmart [B-215030450] Ball Nose 2 Flute Nano Blue Coat | Ball Nose | 3 | 2
 |  |  |  |  |  |  | Ball Nose 2 Flute | B-217535450 | ball end mill | yes | 2 | Ti Coated | 3.5 | 4 | 50 | 32 | 9 | 7 |  |  |  |  |  |  |  |  | 3 | 4 | 3.5 |  | SainSmart [B-217535450] Ball Nose 2 Flute Nano Blue Coat | Ball Nose | 3.5 | 2
 |  |  |  |  |  |  | Ball Nose 2 Flute | B-220040450 | ball end mill | yes | 2 | Ti Coated | 4 | 4 | 50 | 32 | 12 | 8 |  |  |  |  |  |  |  |  |  |  |  |  | SainSmart [B-220040450] Ball Nose 2 Flute Nano Blue Coat | Ball Nose | 4 | 2
 |  |  |  |  |  |  | Ball Nose 2 Flute | B-225050650 | ball end mill | yes | 2 | Ti Coated | 5 | 6 | 50 | 32 | 15 | 10 |  |  |  |  |  |  |  |  | 4 | 6 | 5 |  | SainSmart [B-225050650] Ball Nose 2 Flute Nano Blue Coat | Ball Nose | 5 | 2
 |  |  |  |  |  |  | Ball Nose 2 Flute | B-230060650 | ball end mill | yes | 2 | Ti Coated | 6 | 6 | 50 | 32 | 16 | 10 |  |  |  |  |  |  |  |  |  |  |  |  | SainSmart [B-230060650] Ball Nose 2 Flute Nano Blue Coat | Ball Nose | 6 | 2
 |  |  |  |  |  |  |  |  | Fusion 360 Setup |  |  |  |  |  |  |  |  |  |  |  |  |  |  |  |  |  |  |  |  | Vcarve Setup
Pack Description | Website Ref | Pack Qty | Same Varied | Bit Material | SKU | Coating | Individual Description | Product ID | Type | Clockwise | Number of Flutes | Material | Dia | Shaft Dia | OA Length | Length below Holder | Shoulder length | Flute Length | Corner Radius | Taper Angle (One side) | Tip Length | Tip Dia | Tip Angle | Thread Pitch | Number of Teeth | Thread Profile Angle | Shaft Height | Shaft Upper Dia | Shaft Lower Dia | Group Name | Notes | Type | Diameter | Flutes | Tip Radius | Included Angle | Side Angle | Flat Diameter | Tooth Height | Tooth Size | Tooth Offset | Neck Length
Genmitsu CNC Long Neck Ball Nose End Mill |  |  | Single | Tungsten Carbide Steel Alloy | 101-60-NBLB-0(1-5) | Nano Blue Coat | Long neck Ball Nose 2 Flute | LB-205010450 | ball end mill | yes | 2 | Ti Coated | 1 | 4 | 50 | 32 | 4 | 3 |  |  |  |  |  |  |  |  | 8 | 4 | 1 | SainSmart [101-60-NBLB-0x] Long Neck Ball Nose 2 Flute | SainSmart [LB-205010450] Long neck Ball Nose 2 Flute Nano Blue Coat | Ball Nose | 1 | 2
 | Images |  |  |  |  |  | Long neck Ball Nose 2 Flute | LB-207515450 | ball end mill | yes | 2 | Ti Coated | 1.5 | 4 | 50 | 32 | 6 | 5 |  |  |  |  |  |  |  |  | 5 | 4 | 1.5 |  | SainSmart [LB-207515450] Long neck Ball Nose 2 Flute Nano Blue Coat | Ball Nose | 1.5 | 2
 |  |  |  |  |  |  | Long neck Ball Nose 2 Flute | LB-210020450 | ball end mill | yes | 2 | Ti Coated | 2 | 4 | 50 | 32 | 7.5 | 6 |  |  |  |  |  |  |  |  | 6.5 | 4 | 2 |  | SainSmart [LB-210020450] Long neck Ball Nose 2 Flute Nano Blue Coat | Ball Nose | 2 | 2
 |  |  |  |  |  |  | Long neck Ball Nose 2 Flute | LB-215030450 | ball end mill | yes | 2 | Ti Coated | 3 | 4 | 50 | 32 | 10 | 9 |  |  |  |  |  |  |  |  | 5 | 4 | 3 |  | SainSmart [LB-215030450] Long neck Ball Nose 2 Flute Nano Blue Coat | Ball Nose | 3 | 2
 |  |  |  |  |  |  | Long neck Ball Nose 2 Flute | LB-220040650 | ball end mill | yes | 2 | Ti Coated | 4 | 4 | 50 | 32 | 10.5 | 9 |  |  |  |  |  |  |  |  |  |  |  |  | SainSmart [LB-220040650] Long neck Ball Nose 2 Flute Nano Blue Coat | Ball Nose | 4 | 2
 |  |  |  |  |  |  |  |  | Fusion 360 Setup |  |  |  |  |  |  |  |  |  |  |  |  |  |  |  |  |  |  |  |  | Vcarve Setup
Pack Description | Website Ref | Pack Qty | Same Varied | Bit Material | SKU | Coating | Individual Description | Product ID | Type | Clockwise | Number of Flutes | Material | Dia | Shaft Dia | OA Length | Length below Holder | Shoulder length | Flute Length | Corner Radius | Taper Angle (One side) | Tip Length | Tip Dia | Tip Angle | Thread Pitch | Number of Teeth | Thread Profile Angle | Shaft Height | Shaft Upper Dia | Shaft Lower Dia | Group Name | Notes | Type | Diameter | Flutes | Tip Radius | Included Angle | Side Angle | Flat Diameter | Tooth Height | Tooth Size | Tooth Offset | Neck Length
Genmitsu CNC Corner Radius End Mill |  |  | Single | Tungsten Carbide Steel Alloy | 101-60-NBR-0(1-5) | Nano Blue Coat | Corner Radius 4 Flute | R-405030450 | bull nose end mill | yes | 4 | Ti Coated | 3 | 4 | 50 | 32 | 9 | 7.5 | 0.5 |  |  |  |  |  |  |  | 4 | 4 | 3 | SainSmart [101-60-NBR-0x] Corner Radius 4 Flute | SainSmart [R-405030450] Corner Radius 4 Flute Nano Blue Coat | Radiused End Mill | 3 | 4 | 0.5
 | Images |  |  |  |  |  | Corner Radius 4 Flute | R-405040450 | bull nose end mill | yes | 4 | Ti Coated | 4 | 4 | 50 | 32 | 11 | 9 | 0.5 |  |  |  |  |  |  |  |  |  |  |  | SainSmart [R-405040450] Corner Radius 4 Flute Nano Blue Coat | Radiused End Mill | 4 | 4 | 0.5
 |  |  |  |  |  |  | Corner Radius 4 Flute | R-410040450 | bull nose end mill | yes | 4 | Ti Coated | 4 | 4 | 50 | 32 | 13 | 10 | 1 |  |  |  |  |  |  |  |  |  |  |  | SainSmart [R-410040450] Corner Radius 4 Flute Nano Blue Coat | Radiused End Mill | 4 | 4 | 1
 |  |  |  |  |  |  | Corner Radius 4 Flute | R-405060650 | bull nose end mill | yes | 4 | Ti Coated | 6 | 6 | 50 | 32 | 18 | 15 | 0.5 |  |  |  |  |  |  |  |  |  |  |  | SainSmart [R-405060650] Corner Radius 4 Flute Nano Blue Coat | Radiused End Mill | 6 | 4 | 0.5
 |  |  |  |  |  |  | Corner Radius 4 Flute | R-410060650 | bull nose end mill | yes | 4 | Ti Coated | 6 | 6 | 50 | 32 | 18 | 15 | 1 |  |  |  |  |  |  |  |  |  |  |  | SainSmart [R-410060650] Corner Radius 4 Flute Nano Blue Coat | Radiused End Mill | 6 | 4 | 1
 |  |  |  |  |  |  |  |  | Fusion 360 Setup |  |  |  |  |  |  |  |  |  |  |  |  |  |  |  |  |  |  |  |  | Vcarve Setup
Pack Description | Website Ref | Pack Qty | Same Varied | Bit Material | SKU | Coating | Individual Description | Product ID | Type | Clockwise | Number of Flutes | Material | Dia | Shaft Dia | OA Length | Length below Holder | Shoulder length | Flute Length | Corner Radius | Taper Angle (One side) | Tip Length | Tip Dia | Tip Angle | Thread Pitch | Number of Teeth | Thread Profile Angle | Shaft Height | Shaft Upper Dia | Shaft Lower Dia | Group Name | Notes | Type | Diameter | Flutes | Tip Radius | Included Angle | Side Angle | Flat Diameter | Tooth Height | Tooth Size | Tooth Offset | Neck Length
Genmitsu 6mm Shank 5-PCS 60° 90° 120° 150°V Groove Router Bits Set, VG05-W01 | VG05A | 5 | Varied | Tungsten Carbide Steel Alloy | 101-60B-010 |  | V Grove Router bit 60Deg 16mm Dia | VG05A | tapered mill/Bull Nose | yes | 2 | HSS | 0.1 | 6 | 49 | 31 | 14 | 14 | 0 | 30 |  |  |  |  |  |  | 0.1 / 3 | 6 / 16 | 16 | SainSmart [VG05A] V Groove Set | SainSmart [VG05A] V Grove Router bit 60Deg 16mm Dia | V-Bit | 16 | 2 |  | 60
 | Images |  |  |  |  |  | V Grove Router bit 90Deg 22mm Dia | VG05A | tapered mill/Bull Nose | yes | 2 | HSS | 0.1 | 6 | 46 | 28 | 11 | 11 | 0 | 45 |  |  |  |  |  |  | 0.1 / 3 | 6 / 22 | 22 |  | SainSmart [VG05A] V Grove Router bit 90Deg 22mm Dia | V-Bit | 22 | 2 |  | 90
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

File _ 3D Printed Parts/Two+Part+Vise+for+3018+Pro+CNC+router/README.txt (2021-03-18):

Two Part Vise for 3018 Pro CNC router by DzikuVx on Thingiverse: https://www.thingiverse.com/thing:4780357

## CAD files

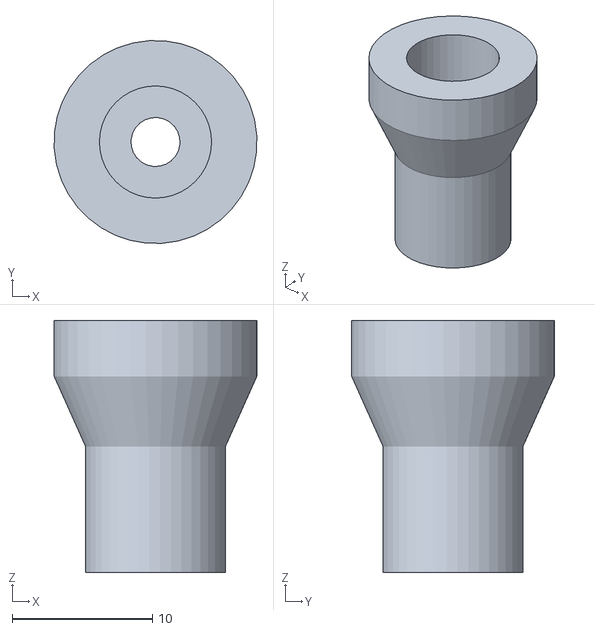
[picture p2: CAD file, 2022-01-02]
_ 3D Printed Parts/Axis Handles/F81TT0SJKN8OX4V.stl
14.5 x 14.5 x 18.0

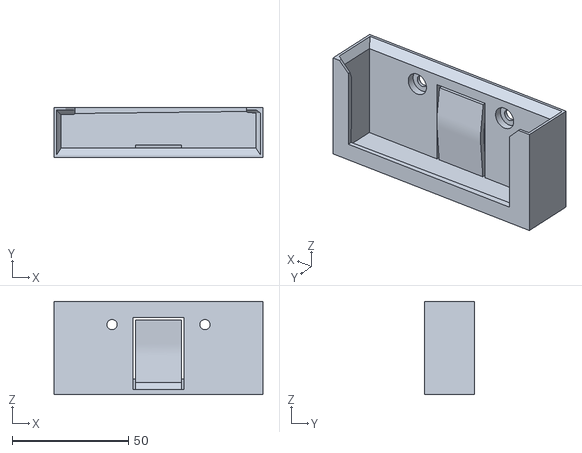
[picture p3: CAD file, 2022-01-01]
_ 3D Printed Parts/CNC3018_OcHolder_NoTools.stl
90.0 x 21.5 x 40.1

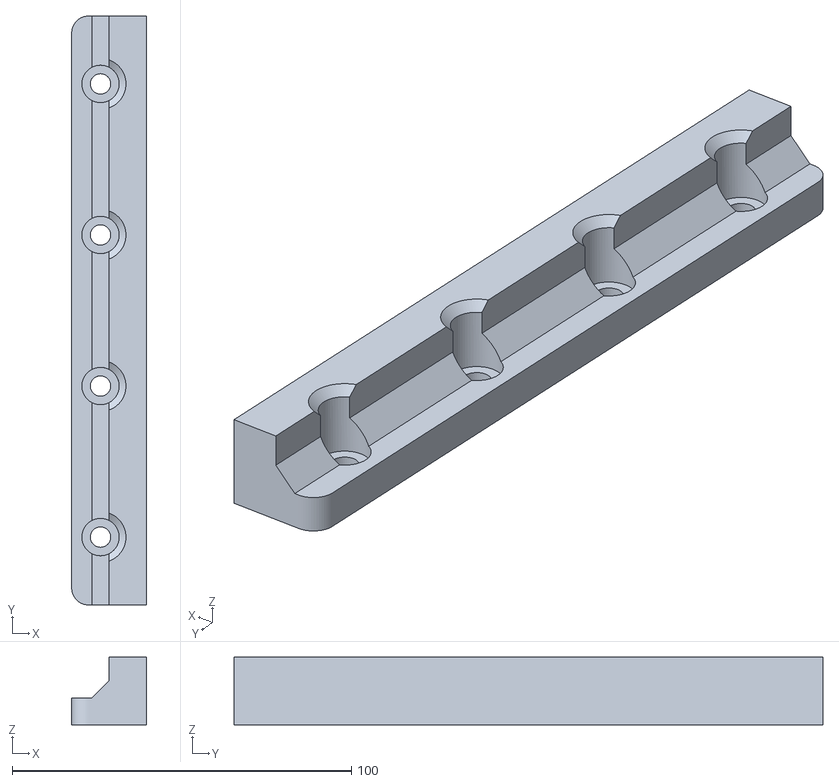
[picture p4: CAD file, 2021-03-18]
_ 3D Printed Parts/Two+Part+Vise+for+3018+Pro+CNC+router/files/Two_Part_Vise_Jaw_A.stl
22.0 x 173.5 x 20.0

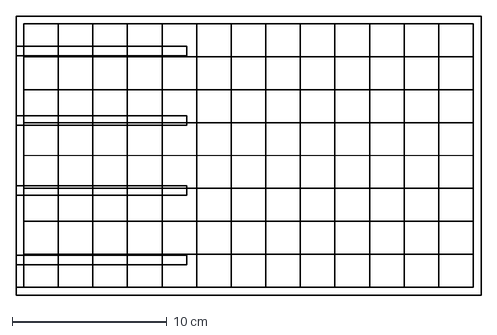
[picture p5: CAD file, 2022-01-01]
_ Setup Guides/Making a Spoilboard/Introduction to CNC for a Total Novice - Making a Spoilboard/Universal Spoilboard.dxf
30.0 x 18.0 cm

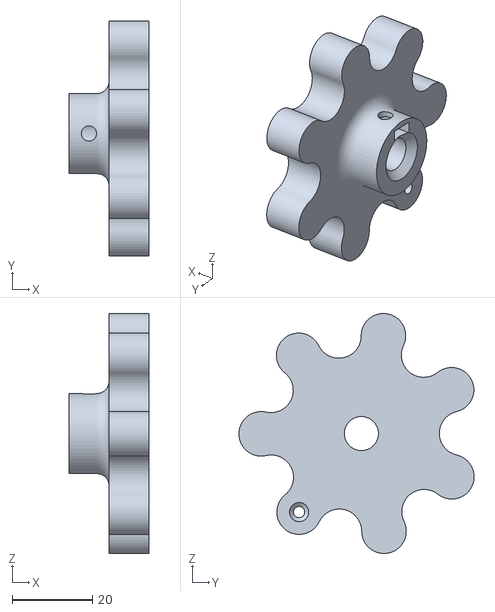
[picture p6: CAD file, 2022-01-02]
_ 3D Printed Parts/Axis Handles/F7LGJAFJKN8OX4U.stl
20.0 x 58.7 x 59.9

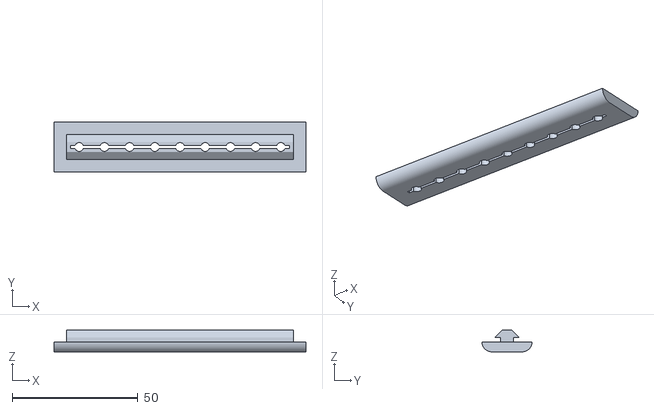
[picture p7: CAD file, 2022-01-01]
_ 3D Printed Parts/CNC_3018_Milling_Bits_Holder.stl
100.0 x 20.0 x 8.60

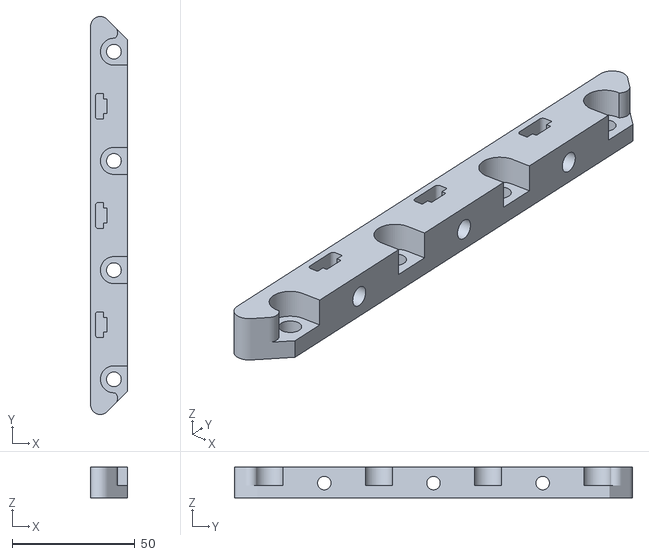
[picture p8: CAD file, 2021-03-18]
_ 3D Printed Parts/Two+Part+Vise+for+3018+Pro+CNC+router/files/Two_Part_Vise_Jaw_B_Base.stl
15.0 x 162.2 x 12.5

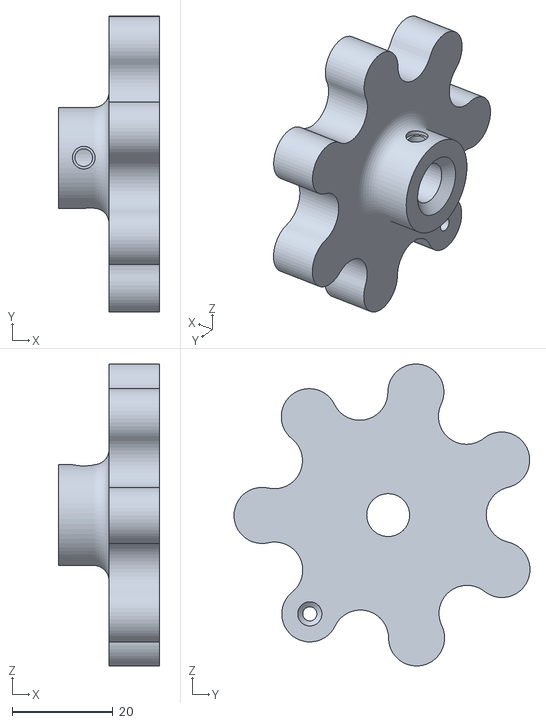
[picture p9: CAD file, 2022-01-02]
_ 3D Printed Parts/Axis Handles/F29MWMZJKN8OX4T.stl
20.0 x 58.7 x 59.9

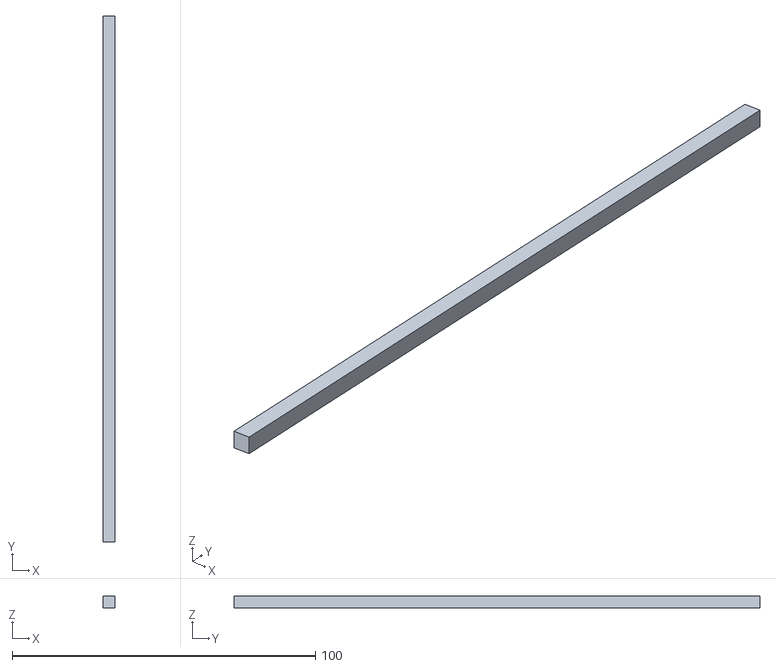
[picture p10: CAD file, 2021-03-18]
_ 3D Printed Parts/Two+Part+Vise+for+3018+Pro+CNC+router/files/Pseudo_Parallel_A.stl
4.00 x 173.5 x 4.00

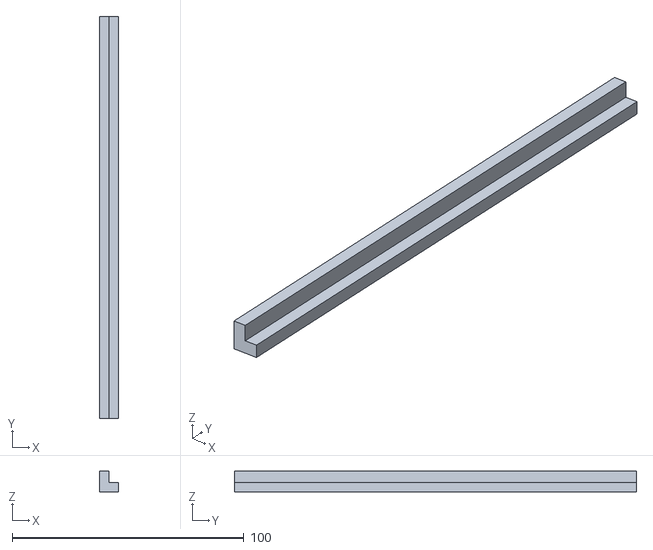
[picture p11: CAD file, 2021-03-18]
_ 3D Printed Parts/Two+Part+Vise+for+3018+Pro+CNC+router/files/Pseudo_Parallel_B.stl
8.00 x 173.5 x 9.00

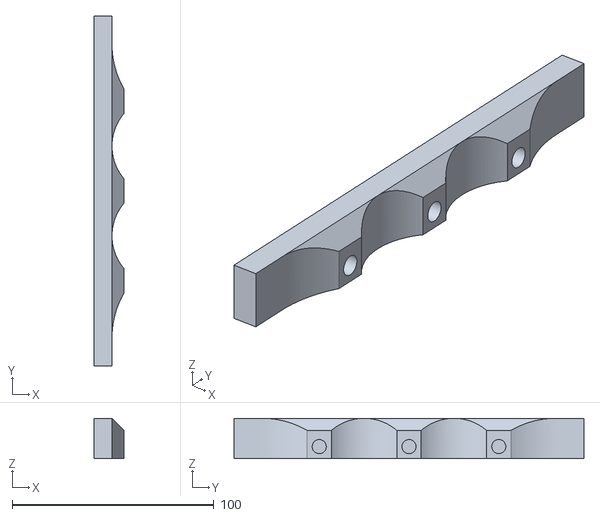
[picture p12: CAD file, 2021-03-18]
_ 3D Printed Parts/Two+Part+Vise+for+3018+Pro+CNC+router/files/Two_Part__Vise_Jaw_B_Block.stl
15.0 x 173.5 x 20.0

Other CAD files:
_ Setup Guides/Making a Spoilboard/Introduction to CNC for a Total Novice - Making a Spoilboard (1)/Universal Spoilboard.f3d
_ Setup Guides/Making a Spoilboard/Introduction to CNC for a Total Novice - Making a Spoilboard/Universal Spoilboard.f3d

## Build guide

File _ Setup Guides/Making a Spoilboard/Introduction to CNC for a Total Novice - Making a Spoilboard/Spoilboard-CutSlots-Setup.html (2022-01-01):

# Setup Sheet for Program Spoilboard-CutSlots

Program Comment:

Cut 4 slots on the spoilboard

Job Description:

CutSlots

Document Path:

Universal Spoilboard

Setup

WCS
: #0

Stock
:

DX: 180mm

DY: 300mm

DZ: 6mm

Part
:

DX: 180mm

DY: 300mm

DZ: 6mm

Stock Lower in WCS #0
:

X: -90mm

Y: 0mm

Z: -6mm

Stock Upper in WCS #0
:

X: 90mm

Y: 300mm

Z: 0mm

Total

Number Of Operations:

1

Number Of Tools:

1

Tools:

T1

Maximum Z:

10mm

Minimum Z:

-7mm

Maximum Feedrate:

500mm/min

Maximum Spindle Speed:

10000rpm

Cutting Distance:

11652.1mm

Rapid Distance:

276.63mm

Estimated Cycle Time:

23m:37s

Tools

T1 D1 L1

Manual tool change

Type:

flat end mill

Diameter:

3.17mm

Length:

21mm

Flutes:

2

Description:

Router, HSS Coated, 2 Flute

Vendor:

SainSmart

Product:

SKU: 101-60-70C15 (https://www.sainsmart.com/collections/cnc/drills)

Minimum Z:

-7mm

Maximum Feed:

500mm/min

Maximum Spindle Speed:

10000rpm

Cutting Distance:

11652.1mm

Rapid Distance:

276.63mm

Estimated Cycle Time:

23m:22s

Holder:

ER11 Collet

Vendor:

SainSmart

Product:

SKU: 101-60-70ER11

Operations

Operation 1/1

Description:

Spoilboard-Cut Slots

Strategy:

Pocket 2D

WCS:

#0

Tolerance:

0.1mm

Stock to Leave:

0mm

Maximum stepdown:

1mm

Maximum stepover:

3mm

Maximum Z:

10mm

Minimum Z:

-7mm

Maximum Spindle Speed:

10000rpm

Maximum Feedrate:

500mm/min

Cutting Distance:

11652.1mm

Rapid Distance:

276.63mm

Estimated Cycle Time:

23m:22s

Coolant:

Off

T1 D1 L1

Manual tool change

Type:

flat end mill

Diameter:

3.17mm

Length:

21mm

Flutes:

2

Description:

Router, HSS Coated, 2 Flute

Vendor:

SainSmart

Product:

SKU: 101-60-70C15 (https://www.sainsmart.com/collections/cnc/drills)

Generated by Fusion 360 CAM 2.0.7813 (http://cam.autodesk.com) Saturday, March 21, 2020 10:48:38

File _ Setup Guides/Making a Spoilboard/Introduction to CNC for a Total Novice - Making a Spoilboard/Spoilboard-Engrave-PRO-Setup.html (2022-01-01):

# Setup Sheet for Program Spoilboard-Engrave

Program Comment:

Engrave Alignment grid on a spoilboard

Job Description:

Engrave

Document Path:

Universal Spoilboard

Setup

WCS
: #0

Stock
:

DX: 300mm

DY: 180mm

DZ: 6mm

Part
:

DX: 300mm

DY: 180mm

DZ: 6mm

Stock Lower in WCS #0
:

X: -5mm

Y: -5mm

Z: -6mm

Stock Upper in WCS #0
:

X: 295mm

Y: 175mm

Z: 0mm

Total

Number Of Operations:

1

Number Of Tools:

1

Tools:

T1

Maximum Z:

10mm

Minimum Z:

-0.2mm

Maximum Feedrate:

500mm/min

Maximum Spindle Speed:

10000rpm

Cutting Distance:

4573.2mm

Rapid Distance:

575.24mm

Estimated Cycle Time:

9m:33s

Tools

T1 D1 L1

Manual tool change

Type:

countersink

Diameter:

3.17mm

Tip Angle:

20°

Length:

11.85mm

Flutes:

1

Description:

V Bit 20˚, HSS

Vendor:

SainSmart

Product:

Supplied with Router

Minimum Z:

-0.2mm

Maximum Feed:

500mm/min

Maximum Spindle Speed:

10000rpm

Cutting Distance:

4573.2mm

Rapid Distance:

575.24mm

Estimated Cycle Time:

9m:18s

Holder:

ER11 Collet

Vendor:

SainSmart

Product:

SKU: 101-60-70ER11

Operations

Operation 1/1

Description:

Spoilboard-Engrave

Strategy:

3D Path

WCS:

#0

Tolerance:

0.01mm

Stock to Leave:

0mm

Maximum Z:

10mm

Minimum Z:

-0.2mm

Maximum Spindle Speed:

10000rpm

Maximum Feedrate:

500mm/min

Cutting Distance:

4573.2mm

Rapid Distance:

575.24mm

Estimated Cycle Time:

9m:18s

Coolant:

Off

T1 D1 L1

Manual tool change

Type:

countersink

Diameter:

3.17mm

Tip Angle:

20°

Length:

11.85mm

Flutes:

1

Description:

V Bit 20˚, HSS

Vendor:

SainSmart

Product:

Supplied with Router

Generated by Fusion 360 CAM 2.0.7813 (http://cam.autodesk.com) Saturday, March 21, 2020 10:57:48

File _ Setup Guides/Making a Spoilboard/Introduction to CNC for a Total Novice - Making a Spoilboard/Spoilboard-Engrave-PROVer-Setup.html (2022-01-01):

# Setup Sheet for Program Spoilboard-Engrave

Program Comment:

Engrave Alignment grid on a spoilboard

Job Description:

Engrave

Document Path:

Universal Spoilboard

Setup

WCS
: #0

Stock
:

DX: 300mm

DY: 180mm

DZ: 6mm

Part
:

DX: 300mm

DY: 180mm

DZ: 6mm

Stock Lower in WCS #0
:

X: -11.5mm

Y: -12mm

Z: -6mm

Stock Upper in WCS #0
:

X: 288.5mm

Y: 168mm

Z: 0mm

Total

Number Of Operations:

1

Number Of Tools:

1

Tools:

T1

Maximum Z:

10mm

Minimum Z:

-0.2mm

Maximum Feedrate:

500mm/min

Maximum Spindle Speed:

10000rpm

Cutting Distance:

4168.2mm

Rapid Distance:

536.15mm

Estimated Cycle Time:

8m:44s

Tools

T1 D1 L1

Manual tool change

Type:

countersink

Diameter:

3.17mm

Tip Angle:

20°

Length:

11.85mm

Flutes:

1

Description:

V Bit 20˚, HSS

Vendor:

SainSmart

Product:

Supplied with Router

Minimum Z:

-0.2mm

Maximum Feed:

500mm/min

Maximum Spindle Speed:

10000rpm

Cutting Distance:

4168.2mm

Rapid Distance:

536.15mm

Estimated Cycle Time:

8m:29s

Holder:

ER11 Collet

Vendor:

SainSmart

Product:

SKU: 101-60-70ER11

Operations

Operation 1/1

Description:

Spoilboard-Engrave

Strategy:

3D Path

WCS:

#0

Tolerance:

0.01mm

Stock to Leave:

0mm

Maximum Z:

10mm

Minimum Z:

-0.2mm

Maximum Spindle Speed:

10000rpm

Maximum Feedrate:

500mm/min

Cutting Distance:

4168.2mm

Rapid Distance:

536.15mm

Estimated Cycle Time:

8m:29s

Coolant:

Off

T1 D1 L1

Manual tool change

Type:

countersink

Diameter:

3.17mm

Tip Angle:

20°

Length:

11.85mm

Flutes:

1

Description:

V Bit 20˚, HSS

Vendor:

SainSmart

Product:

Supplied with Router

Generated by Fusion 360 CAM 2.0.7813 (http://cam.autodesk.com) Saturday, March 21, 2020 11:31:56

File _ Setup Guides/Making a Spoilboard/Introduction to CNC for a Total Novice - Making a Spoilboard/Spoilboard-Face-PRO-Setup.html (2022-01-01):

# Setup Sheet for Program Spoilboard-Face

Program Comment:

Skim 0.2mm off the top of the spoilboard to level it

Job Description:

Face

Document Path:

Universal Spoilboard

Setup

WCS
: #0

Stock
:

DX: 300mm

DY: 180mm

DZ: 6.2mm

Part
:

DX: 300mm

DY: 180mm

DZ: 6mm

Stock Lower in WCS #0
:

X: -5mm

Y: -5mm

Z: -6mm

Stock Upper in WCS #0
:

X: 295mm

Y: 175mm

Z: 0.2mm

Total

Number Of Operations:

1

Number Of Tools:

1

Tools:

T1

Maximum Z:

10.2mm

Minimum Z:

0mm

Maximum Feedrate:

500mm/min

Maximum Spindle Speed:

10000rpm

Cutting Distance:

10321.95mm

Rapid Distance:

18.4mm

Estimated Cycle Time:

20m:54s

Tools

T1 D1 L1

Manual tool change

Type:

face mill

Diameter:

13mm

Taper Angle:

1°

Length:

14mm

Flutes:

2

Description:

Facing bit

Minimum Z:

0mm

Maximum Feed:

500mm/min

Maximum Spindle Speed:

10000rpm

Cutting Distance:

10321.95mm

Rapid Distance:

18.4mm

Estimated Cycle Time:

20m:39s

Holder:

ER11 Collet

Vendor:

SainSmart

Product:

SKU: 101-60-70ER11

Operations

Operation 1/1

Description:

Spoilboard-Face PRO

Strategy:

Parallel

WCS:

#0

Tolerance:

0.01mm

Stock to Leave:

0mm

Maximum stepover:

5mm

Maximum Z:

10.2mm

Minimum Z:

0mm

Maximum Spindle Speed:

10000rpm

Maximum Feedrate:

500mm/min

Cutting Distance:

10321.95mm

Rapid Distance:

18.4mm

Estimated Cycle Time:

20m:39s

Coolant:

Off

T1 D1 L1

Manual tool change

Type:

face mill

Diameter:

13mm

Taper Angle:

1°

Length:

14mm

Flutes:

2

Description:

Facing bit

Generated by Fusion 360 CAM 2.0.7813 (http://cam.autodesk.com) Saturday, March 21, 2020 10:54:43

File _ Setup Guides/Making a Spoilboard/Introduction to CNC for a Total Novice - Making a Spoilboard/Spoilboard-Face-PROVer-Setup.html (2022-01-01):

# Setup Sheet for Program Spoilboard-Face

Program Comment:

Skim 0.2mm off the top of the spoilboard to level it

Job Description:

Face

Document Path:

Universal Spoilboard

Setup

WCS
: #0

Stock
:

DX: 300mm

DY: 180mm

DZ: 6.2mm

Part
:

DX: 300mm

DY: 180mm

DZ: 6mm

Stock Lower in WCS #0
:

X: -11.5mm

Y: -12mm

Z: -6mm

Stock Upper in WCS #0
:

X: 288.5mm

Y: 168mm

Z: 0.2mm

Total

Number Of Operations:

1

Number Of Tools:

1

Tools:

T1

Maximum Z:

10.2mm

Minimum Z:

0mm

Maximum Feedrate:

200mm/min

Maximum Spindle Speed:

10000rpm

Cutting Distance:

4500.9mm

Rapid Distance:

18.4mm

Estimated Cycle Time:

22m:45s

Tools

T1 D1 L1

Manual tool change

Type:

face mill

Diameter:

25mm

Taper Angle:

2°

Length:

14mm

Flutes:

3

Description:

Facing bit

Vendor:

ebay

Minimum Z:

0mm

Maximum Feed:

200mm/min

Maximum Spindle Speed:

10000rpm

Cutting Distance:

4500.9mm

Rapid Distance:

18.4mm

Estimated Cycle Time:

22m:30s

Holder:

ER11 Collet

Vendor:

SainSmart

Product:

SKU: 101-60-70ER11

Operations

Operation 1/1

Description:

Spoilboard-Face PROVer

Strategy:

Parallel

WCS:

#0

Tolerance:

0.01mm

Stock to Leave:

0mm

Maximum stepover:

10mm

Maximum Z:

10.2mm

Minimum Z:

0mm

Maximum Spindle Speed:

10000rpm

Maximum Feedrate:

200mm/min

Cutting Distance:

4500.9mm

Rapid Distance:

18.4mm

Estimated Cycle Time:

22m:30s

Coolant:

Off

T1 D1 L1

Manual tool change

Type:

face mill

Diameter:

25mm

Taper Angle:

2°

Length:

14mm

Flutes:

3

Description:

Facing bit

Vendor:

ebay

Generated by Fusion 360 CAM 2.0.7813 (http://cam.autodesk.com) Saturday, March 21, 2020 11:27:38

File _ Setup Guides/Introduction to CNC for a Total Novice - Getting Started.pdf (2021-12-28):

Introduction to CNC for a Total Novice - Getting Started V2.1 August 2020

# Introduction to CNC for a Total Novice

Part of a series by Graham Bland

## Getting Started

## Contents

## Changes

From V1.0

- Stripped out the Laser bits into a separate document
- Tried to make it a bit less rambling and more linear
- Added Assembly hints and post assembly checks
- Expanded and added Examples for coordinate systems
- Updated and expanded due to learning and understanding more as I progress

From V2.0

- Corrected the section “Changing the direction of movement on an axis” which had instructions for the X and Z axes reversed. (My thanks to Anthony Drake for pointing this out)

## Introduction

If you are a novice this is for you, if not then there may be bits of interest, if you know what you are doing any comments would be welcome!

My apologies for this but when I started this was a series of five pages of notes I had made when starting out as a total novice. Now It’s 30+ pages because as I keep on learning there is more to add!

A while ago I decided to take the plunge and I purchased a SainSmart Genimitsu 3018-PRO with a 2.5W 450nm Laser module and a full set of bits from SainSmart. I later upgraded to a 5.5W Laser.

Any comments or specific examples refer to my SainSmart Genimitsu 3018-PRO using the Grbl system, although a lot does apply to other models, yours may be different. A lot of information is anecdotal and based on reading the forums and from the internet.

But I do hope this series is useful for anyone using any hobbyist CNC router for the first time.

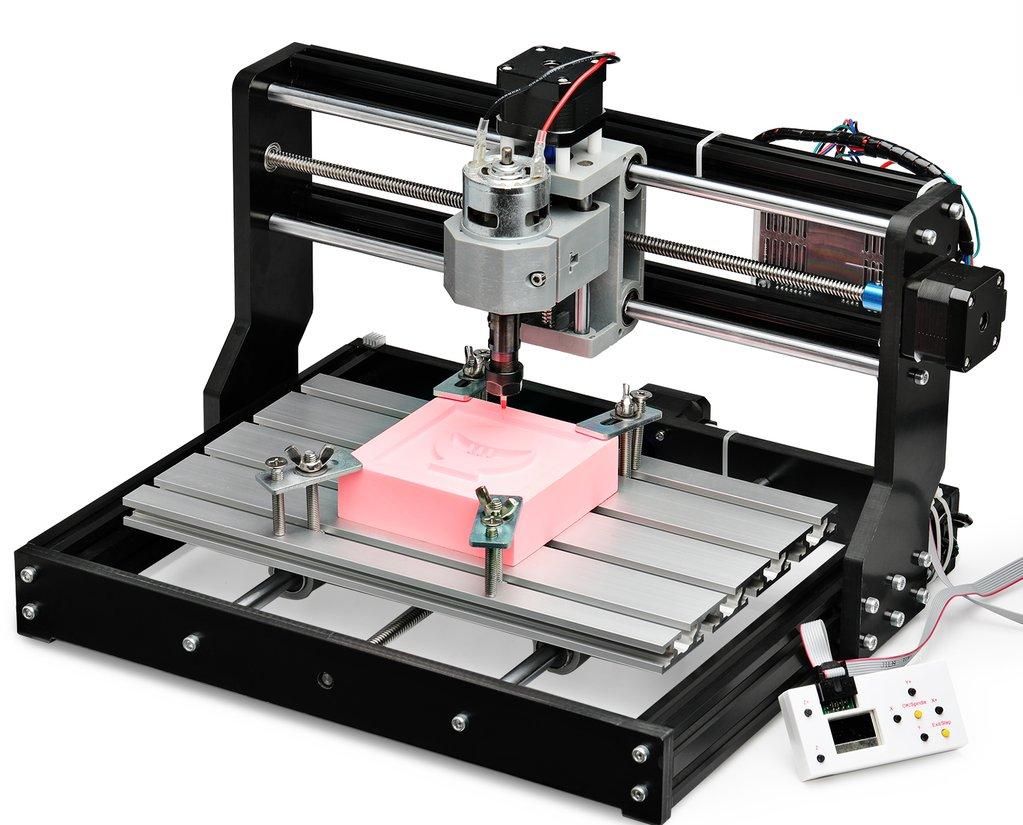
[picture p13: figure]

There are other suppliers selling under the same name of 3018, 3018-PRO | These, while looking
and sounding the same will differ in the details, the router motherboard being different, if an adjustable collet is fitted to the Spindle...... The 3018 simply means 30cm x 18cm dimensions of the bed, without the spaces, cm and x, just the travel on the X and Y axis. There are other variants such as 2415...... which follow the same naming conventions.

I am using free to use software here by preference (Apart from Windows of course). NOTE: I mean free to use for me as a non commercial hobbyist, for example I am using Autodesk Fusion360 and have a free licence as long as I don’t try and make any money out of it, that’s fine as a full licence would be hundreds of pounds a year and it’s a hobby. Any software which has a free version and a subscription version, well I am referring to the free one unless specified.

I am producing this as a document, mainly because It is an edited series of notes I made, partly because I am tired of watching instructional videos on YouTube which play at Mach 2 and so I am constantly stopping, rewinding and re-watching. Also I have been told I have a body made for Radio, a voice most suited to the Deaf and I still haven’t worked out how to use the video camera on my phone properly.

### My Background

- I am a retired IT guy, started as a trainee programmer using an IBM 360/40 a long, long time ago (the /40 designation meant it had a 40k memory, massive at that time).

- Until recently if I wanted to design something I would use pencils, paper, compass and ruler.
- I did get 98% on my last woodwork exam and the table I made is still in use, but that was an even longer, long time ago.
- Always been keen on making things and trying to understand how things work.

### Disclaimer

Yeah nowadays it has to be included, and it makes sense as I accept NO liability for anything I may say, write or think.

1. I am a total novice (or was when I started out). I MAKE NO CLAIM THAT ANYTHING I SAY IS CORRECT! All this is based on searching the Internet, forum comments.... and my own experiences.
2. If you have and are using a Laser module, even the lowest powered is powerful enough to destroy your vision completely, and that of any pets, children, spectators etc. SO EXCLUDE THEM AND USE THE GOGGLES!
3. These are power tools, sharp pieces of metal designed to cut things while rotating at high speed and throwing small bits away also at high speed. Keep everybody’s fingers out! A wood chip flying up your nose is nothing to be sneezed at, never mind in one of your eyes.
4. Take account of the materials you are using and take adequate precautions, dust and ashes can be harmful.
5. I work in mm. Why anyone still uses inches for design work is a mystery. But then I still think of temperatures in Fahrenheit, anything beyond 500m in miles and property plot sizes in acres!
6. I have been told by lots of people that my sense of humour is at the least a bit strange. I do not apologise for it.
7. Any corrections, clarifications or discussion welcome. You can find me on the Facebook SainSmart Genmitsu CNC Routers Group as Graham Bland. https://www.facebook.com/groups/SainSmart.GenmitsuCNC/

### Accompanying files

NOTE: Facebook has a problem, it will not allow compressed (.zip, .gz, ......) to be uploaded to the Files section of any group, but it bases this decision solely on the file extension, not the contents.

It is easy to bypass this by changing the file extension before uploading, I use .zip files, and rename them to .zipp This means that after downloading you will have to reverse this by renaming any xx.zipp file to xx.zip, windows will issue warnings that you are probably going to make the file unusable, just ignore it and rename anyway. Then you can open and extract the files as you wish.

So you there may be 2 versions in the files section. One an xx.pdf which is the basic words, and if there are any accompanying files with it an xx.zipp the .pdf and everything else.

Accompanying files for this section are:

BitPositioner.pdf | A sheet of bit positioning aids as a PDF
SingleBitPositioner.jpg | Picture of one bit positioning aid

3018-PRO Specifications.

Derived from a number of sources, but as far as I can determine, at the time of writing.

NOTE: Specifications can and will change, to be honest some values are just my best guesses.

X Travel (mm) | 300
Y Travel (mm) | 180
Z Travel (mm) | 45
Bed Size X (mm) | 290

Bed Size Y (mm) | 180
Resolution X (mm) | 0.01
Resolution Y (mm) | 0.01
Resolution Z (mm) | 0.01
Max Feed Rate X (mm/min) | 1000
Max Feed Rate Y (mm/min) | 1000
Max Feed Rate Z (mm/min) | 1000
Router bit Holder | ER 11
Std bit Shank (mm) | 3.175
Min bit Shank (mm) (Requires collet set) | 1
Max bit Shank (mm) (Requires collet set) | 7
Spindle Motor | Brushed, Type 775
Max Spindle Speed (RPM at 24V No Load) | ~8,500
Max Torque (N/m) | 0.2
Supply (V) | 24V (on this router)
Stepper Motors | Nema 17 Bipolar
Rotation Degrees per step | 1.8˚
Steps per rotation | 200
Torque (Nm) | 0.25
Supply (V) | 12
Current (A) | 1.3
Max RPM (Depends on Motor controller) | 500
Threaded screws (mm per rotation) | 2

Laser 2.5W and 5.5W
Type | Blue Diode
Frequency nM | 450
Recommended Focal Length mm | 50

One thing to remember, these are hobby machines, inexpensive hobby machines, the main drive for the development of CNC is commercial manufacturing. If you are expecting to spend £200 on a router you cannot really expect the same construction, tolerances and features you would get if you were spending £2,000 or £20,000 on the machine. But the principles involved are the same.

## Assembling your router

I’m not really going to get far into this as there are loads of YouTube videos and other tutorials available, apart from a couple of hints.

These machines change in the details over time, to improve the quality, solve problems and decrease the costs, so the video may not exactly match what you have.

- Clean out any swarf from the machining of the holes as best you can.

- Wipe any excess oil from all parts.
- Lubricate the guide rods and threaded screws with a little dry spray lubricant. Routing is a messy business and using a dry lubricant helps stop things sticking to the rods and screws.
- Aligning the Gantry is quite critical, mainly on getting it straight and vertical; my instructions were to make it 46.5mm from the end of the side members, tricky to do using a ruler and square when you get to it.
- Before you assemble the frame take a square and a sharp knife, measure the 46.5mm in from the end and make a small mark on one of them.
- Align the 2 side members on a flat surface one above the other using the square at the ends.
- Take the square and scribe a thin vertical line across them both using the measured mark.
- Make sure the line is at the same end and on the outside when putting in the sides.
- Align the gantry edge to the line on both sides. This ensures it is both at the correct distance and vertical.
- When finally tightening the frame bolts make sure you do it on a flat surface to get the frame as level as you can.
- Things may have more grub screws than the instructions suggest. Loosen and then tighten them all!
- I strongly suggest applying a drop of thread lock to all screws, especially the grub screws to prevent them from vibrating loose over time.
- When tie wrapping the cables make sure they don’t stick up between the frame top and the bottom of the bed, there is not a lot of clearance here, enough for a tie wrap, but not the head of it.
- Instructions may say the Spindle Motor has a red dot on it to show which way it should be connected. A lot don’t have a red dot but have a very faint + mark on one of the plastic dots instead.
- The spindle motor can be a very tight fit! Slacken off the bolt, if it is difficult to fit in then use the end of one of the collet spanners to gently prise it open until you can get the motor in.
- Align the top of the sleeve around the motor with the top of the motor bracket before tightening it up. This seems to be a good starting position.
- Do check that all the axes move freely to their limits in all directions without binding by turning the threaded rods manually (without any power connected to the router).

## Checking it out

These are some simple checks to make once assembly is complete, but before you have tie wrapped or secured all the wiring, just in case you need to change any of it.

A lot of suppliers don’t seem to take a lot of care with the default settings on the motherboard (described later), amongst other things these control the direction the axes will move in and how far they will travel. I have never seen examples of a problem with any supplied by SainSmart but quite a few from others.

What we are going to test is:

- Do the settings on the router make sense?
- Are the axes connected correctly?
- Does the spindle turn in the correct direction?
- Is the direction of movement on each axis correct?
- Is the distance travelled by each axis correct?

It is best to start these checks with the spindle above the centre of the bed and at the midpoint on the Z axis, manually adjust it by turning the threaded rods before powering on for the first time.

Install Candle on your computer, it should be supplied with your router but if not you can download it for Windows from http://s3.amazonaws.com/s3.image.smart/download/101-60-280PRO/Grblcontrol%28Candle_1.1.7%20%29.zip (http://s3.amazonaws.com/s3.image.smart/download/101-60-280PRO/Grblcontrol%28Candle_1.1.7%20%29.zip) or https://github.com/Denvi/Candle/releases Extract and install. NOTE: There is a later release than 1.1.7, version 1.2b but at the time of writing this is still a pre-release version.

Connect the computer to the Router via the USB cable and plug it in.

Start Candle and connect to the Router, it should find it automatically, if not click on Service/Settings you can select the Com Port there.

You should see something like this from Candle 1.17:

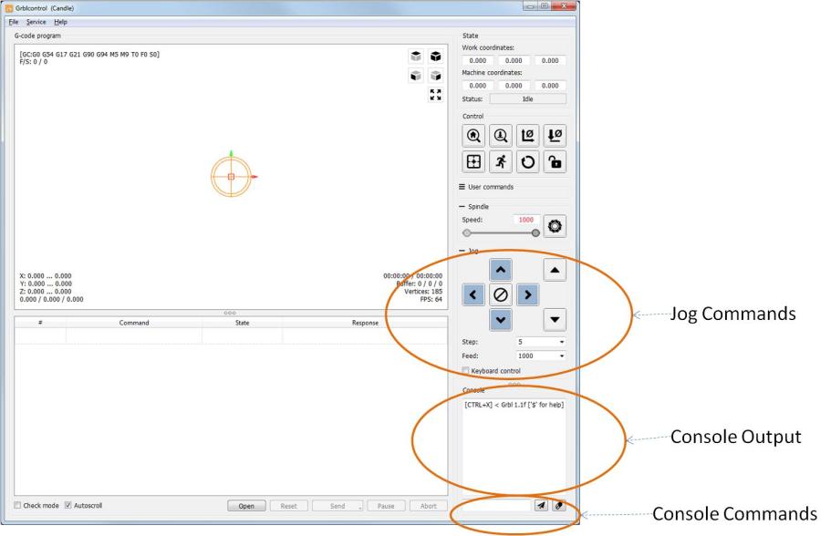
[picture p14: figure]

The first thing to do is to type $$ in the Console command box and send it by hitting the enter key. This will display in the console output all the Grbl settings values from the router. Copy these into a text editor and save the file somewhere as a baseline. No matter how much you may mess up the settings you will always then have a previous set to go back to.

You will see the response to the $$ command as a list of $99=xx lines where 99 is the setting number and xx is the current value.

To change a value send the command of $99=xxx where 99 is the setting number and xxx is the value. These are permanently stored on the motherboard so they only need to be changed once.

### Sanity check on the Router settings

Some suppliers, well let’s just say they don’t believe in quality control a lot. I have seen many examples where some of the router settings are crazy.

The motherboard has a series of settings on it; these allow it to be used on different routers, different stepper motors, different wiring etc. Nearly all of these should be static, set once at the factory to suit the router and then forget they are there, but for example if you were to add limit switches to enable home positioning or to buy a replacement motherboard, which is not set up for your specific router some of them would have to be changed.

Remember there is no correct answer, some routers and motherboards are different, new versions are developed which means these can change over time but a quick sanity check of the important ones makes sense. I have listed the settings and given a range which I think they should be in or a suggested value.

NOTE: If I say something should be 0.01 ish and your default settings are for example 0.05 or 0.02 don’t worry. If your default value is something like 25483.72 then it is almost certainly wrong! If the Range says ‘Only’ and your value is different then it is wrong (probably)!

The default settings and values for my 3018-PRO with a Woodpecker CamXTool 3.4 motherboard :

Applies only if using Soft Limits in conjunction with limit switches
Applies only if using limit switches
Default Setting | Description (The links will take you to the relevant page for Grbl 1.1) | Range
$0=10 | Step pulse, microseconds (https://github.com/gnea/grbl/wiki/Grbl-v1.1-Configuration#0--step-pulse-microseconds) | 3-15 ish (only the 15 is ish)
$1=25 | Step idle delay, milliseconds (https://github.com/gnea/grbl/wiki/Grbl-v1.1-Configuration#1---step-idle-delay-milliseconds) | 15-30 ish OR 255
$2=0 | Step port invert, mask (https://github.com/gnea/grbl/wiki/Grbl-v1.1-Configuration#2--step-port-invert-mask) | Only 0-7
$3=2 | Direction port invert, mask (https://github.com/gnea/grbl/wiki/Grbl-v1.1-Configuration#3--direction-port-invert-mask) | Only 0-7
$4=0 | Step enable invert, boolean (https://github.com/gnea/grbl/wiki/Grbl-v1.1-Configuration#4---step-enable-invert-boolean) | Only 0 or 1
$5=0 | Limit pins invert, boolean (https://github.com/gnea/grbl/wiki/Grbl-v1.1-Configuration#5----limit-pins-invert-boolean) | Only 0 or 1
$6=0 | Probe pin invert, boolean (https://github.com/gnea/grbl/wiki/Grbl-v1.1-Configuration#6----probe-pin-invert-boolean) | Only 0 or 1
$10=1 | Status report, mask (https://github.com/gnea/grbl/wiki/Grbl-v1.1-Configuration#10---status-report-mask) | Only 0-3
$11=0.010 | Junction deviation, mm (https://github.com/gnea/grbl/wiki/Grbl-v1.1-Configuration#11---junction-deviation-mm) | 0.1 to 0.001 ish
$12=0.002 | Arc tolerance, mm (https://github.com/gnea/grbl/wiki/Grbl-v1.1-Configuration#12--arc-tolerance-mm) | 0.1 to 0.001 ish
$13=0 | Report inches, boolean (https://github.com/gnea/grbl/wiki/Grbl-v1.1-Configuration#13---report-inches-boolean) | Only 0 or 1
$20=0 | Soft limits, boolean (https://github.com/gnea/grbl/wiki/Grbl-v1.1-Configuration#20---soft-limits-boolean) | Only 0 or 1
$21=0 | Hard limits, boolean (https://github.com/gnea/grbl/wiki/Grbl-v1.1-Configuration#21---hard-limits-boolean) | Only 0 or 1
$22=0 | Homing cycle, boolean (https://github.com/gnea/grbl/wiki/Grbl-v1.1-Configuration#22---homing-cycle-boolean) | Only 0 or 1
$23=0 | Homing dir invert, mask (https://github.com/gnea/grbl/wiki/Grbl-v1.1-Configuration#23---homing-dir-invert-mask) | Only 0-7
$24=25.000 | Homing feed, mm/min (https://github.com/gnea/grbl/wiki/Grbl-v1.1-Configuration#24---homing-feed-mmmin) | 10-50 ish
$25=500.000 | Homing seek, mm/min (https://github.com/gnea/grbl/wiki/Grbl-v1.1-Configuration#25---homing-seek-mmmin) | 250-750 ish
$26=250 | Homing debounce, milliseconds (https://github.com/gnea/grbl/wiki/Grbl-v1.1-Configuration#26---homing-debounce-milliseconds) | 5-50 ish Yes I know my default setting is wrong but it is not used.
$27=1.000 | Homing pull-off, mm (https://github.com/gnea/grbl/wiki/Grbl-v1.1-Configuration#27---homing-pull-off-mm) | 0.5-3.5 ish
$30=1000 | Max spindle speed, RPM (https://github.com/gnea/grbl/wiki/Grbl-v1.1-Configuration#30---max-spindle-speed-rpm) | 750-7500 ish
$31=0 | Min spindle speed, RPM (https://github.com/gnea/grbl/wiki/Grbl-v1.1-Configuration#31---min-spindle-speed-rpm) | 0-100 ish

$32=0 | Laser mode, boolean (https://github.com/gnea/grbl/wiki/Grbl-v1.1-Configuration#32---laser-mode-boolean) | 0 or 1 1 ONLY when using a laser
$100=800.000 | X steps/mm (https://github.com/gnea/grbl/wiki/Grbl-v1.1-Configuration#100-101-and-102--xyz-stepsmm) | 800 or 1600*
$101=800.000 | Y steps/mm (https://github.com/gnea/grbl/wiki/Grbl-v1.1-Configuration#100-101-and-102--xyz-stepsmm) | 800 or 1600*
$102=800.000 | Z steps/mm (https://github.com/gnea/grbl/wiki/Grbl-v1.1-Configuration#100-101-and-102--xyz-stepsmm) | 800 or 1600*
$110=1000.000 | X Max rate, mm/min (https://github.com/gnea/grbl/wiki/Grbl-v1.1-Configuration#110-111-and-112--xyz-max-rate-mmmin) | 500-2000 ish
$111=1000.000 | Y Max rate, mm/min (https://github.com/gnea/grbl/wiki/Grbl-v1.1-Configuration#110-111-and-112--xyz-max-rate-mmmin) | 500-2000 ish
$112=600.000 | Z Max rate, mm/min (https://github.com/gnea/grbl/wiki/Grbl-v1.1-Configuration#110-111-and-112--xyz-max-rate-mmmin) | 500-2000 ish
$120=30.000 | X Acceleration, mm/sec^2 (https://github.com/gnea/grbl/wiki/Grbl-v1.1-Configuration#120-121-122--xyz-acceleration-mmsec2) | 20-10000 ish
$121=30.000 | Y Acceleration, mm/sec^2 (https://github.com/gnea/grbl/wiki/Grbl-v1.1-Configuration#120-121-122--xyz-acceleration-mmsec2) | 20-10000 ish
$122=30.000 | Z Acceleration, mm/sec^2 (https://github.com/gnea/grbl/wiki/Grbl-v1.1-Configuration#120-121-122--xyz-acceleration-mmsec2) | 20-10000 ish
$130=200.000 | X Max travel, mm (https://github.com/gnea/grbl/wiki/Grbl-v1.1-Configuration#130-131-132--xyz-max-travel-mm) | Around your router size ish
$131=200.000 | Y Max travel, mm (https://github.com/gnea/grbl/wiki/Grbl-v1.1-Configuration#130-131-132--xyz-max-travel-mm) | Around your router size ish
$132=200.000 | Z Max travel, mm (https://github.com/gnea/grbl/wiki/Grbl-v1.1-Configuration#130-131-132--xyz-max-travel-mm) | Around your router size ish

*
These values ($100-102) should all be the same. If only 2 are the same set the third accordingly. Other values are possible but 800 or 1600 are overwhelmingly common for this sort of router. However the tests you are going to run check these settings.

If you changed anything I suggest you keep a record of it as well as your original settings.

### Recovering your settings

Normally you can reset the machine to its factory settings by sending it:

$RST=$ to erase and restore the $$ Grbl settings back to defaults, which is defined by the default settings file used when compiling Grbl.

Your board manufacturer can disable these commands. And if you have changed anything your changes will be lost! If some of the settings were wrong to start with then these commands will restore all the wrong settings as well. But you can’t have everything!

### Are the axes connected correctly and move in the correct direction

Set the step value in the jog commands area in Candle to 10 using the Step dropdown list, this sets how far the spindle will move in mm each time you click on a jog button, it needs to be something you can see but not move it so far it reaches the edges.

All movements on the axes are the spindle relative to the bed looking from the front. The left and right arrows should move the spindle left and right respectively, the X axis. Up and Down Buttons should move the bed forwards (the bed moves, not the spindle but the spindle gets closer to the top of the work), towards the front, or backwards, away from the front respectively, the Y axis. The two buttons on the right of the Jog commands should move the spindle height up and down respectively, the Z axis.

Lastly in the box above the jog commands set the spindle speed to something like 10 then click on the ‘Circular saw’ icon this should turn the spindle motor on and off.

When turning it should be rotating in a clockwise direction, you should be able to see the direction of rotation if you can’t tell carefully hold a piece of card to an edge of the tool holder and see which direction it is tugged in.

Hopefully everything works as expected but if not:

Troubleshooting
Problem | Possible Solution
Spindle rotates in the wrong direction | Swap the two wires over on the top of the spindle motor.
The wrong axis moves | Check the connections from the stepper motors and make sure they are plugged into the correct X Y and Z axis connection on the router board.
One or more axes move in the wrong direction | This needs a change in the motherboard settings as described below. It is almost certainly NOT a wiring problem.
An axis does not move at all | • | Check the connections, make sure it is plugged in correctly.
- Check that the axis is not binding by turning the screw by
| | hand (disconnect the router first).
- Check that the grub screws on the coupler connecting the
| | threaded rod to the stepper motor are tight and the coupler is not slipping.
- Lastly swap the connection for the stepper motor into the
| | router motherboard for that axis with another one. If it now moves (remember it is now a different axis) and the other one doesn’t then it is likely to be a motherboard failure, or possibly a faulty cable. Swap the cable with a working one just to be sure.

Changing the direction of movement on an axis If anything is moving in the wrong direction then you need to change one of the settings, namely $3, the direction port invert mask to be precise. This is very easy to do.

This is what is known as a bitmask, the low order 3 bits are used to control the directions the axes move (ZYX). Convert the original value of $3 to binary, flip the appropriate bits for any axis moving in the wrong direction and convert back to a decimal number. (the decimal value will always be between 7 and 0 inclusive).

OR use the following table: Select the row for your current $3 value, go across to the column for the Axis to change and the value there is your new $3 value.

NOTE: THIS ONLY ALLOWS YOU TO CHANGE ONE AXIS AT A TIME. If you need to change more than one make multiple passes through the process.

New $3 Value
Current $3 Value | Invert Z | Invert Y | Invert X
0 | 4 | 2 | 1
1 | 5 | 3 | 0
2 | 6 | 0 | 3
3 | 7 | 1 | 2
4 | 0 | 6 | 5
5 | 1 | 7 | 4
6 | 2 | 4 | 7
7 | 3 | 5 | 6

Examples:

Current $3 value is 2 and the X axis needs inverting.
Select the 2 row and the X column, the new $3 value is 3.

Current $3 value is 3, and the Y and Z axes need inverting.
To invert the Y axis select the 3 row and the Y column, the new $3 value is 1. To invert the Z axis select the 1 row and the Z column, the new $3 value is 5.

In Candle type $3=x in the console command box where x is the revised number and hit enter to send it to the router.

If anything has failed or been changed repeat the tests, everything should now be moving in the correct direction, if not repeat the above until it does.

If you changed any settings make a note in your file containing your original settings just in case.

### Distance travelled by each axis

The movement is controlled by the $100, $101 and $102 parameters. Look at the values you got back from the $$ command.

- These values are the number of microsteps required to move the spindle on each axis by 1mm, $100 sets the X axis, $101 - Y, $102 - Z.
- These should all be the same, I have never heard of a machine like this using different values for $100,101 and 102. It would be possible to design and build one but as long as your stepper motors look the same on each of the axes and the threaded rods look the same it is almost certain they should all be the same.
- They are almost certainly going to be whole round numbers.
- NOTE: because of the standard components that tend to be used the likely values on a 3018 are going to probably be 800 or 1600. 324.6 or anything similar is almost certainly going to be wrong.

What they tell the motherboard is how many microsteps it has to turn the threaded rod on the axes to move the spindle 1mm. If they are not all the same then the first step is to send $101/2/3=800/1600 commands to make them all the same (Hint: If two of them are 800 or 1600 select that value!).

Now they are all the same we only need to check one value, I select the X axis.

1. Take a piece of paper, tape, ruler, use a pencil on the bed or just eyeball it.
2. Mark 2 points 10mm apart (10 is not a magic number but it works well) (Make sure you have 10mm of travel available to the right first)
3. Using the jog commands (or move the paper/ruler etc.) position the spindle over the left hand mark.
4. Now set the jog step to 10mm
5. Jog right once
6. The spindle should now be over the second mark.

You are not looking for if it moves 9.9mm instead of 10mm, if it is out it is much more likely to be a gross error, moves 5mm or 20mm instead of 10mm. Estimate how far out it is, if has only got ½ way there then your $100 value should be doubled, if it travelled twice as far as it should then your $100 value should be halved, remember 800 and 1600 are the common values.

I would then suggest a quick visual check by jogging all the axes by 10mm and making sure the distance travelled looks like 10mm.

CONGRATULATIONS! Your router is now initially set up!

### Key Router settings affecting setup of your machine

$30 and $31 – Max and Min Spindle Speed (RPM)
First on these machines this is not actually the RPM of the spindle, the board does not get any feedback on the actual speed so can’t tell and adjust the speed. It’s just a range of power using PWM sent to the spindle motor or laser. This is not an exact linear mapping (500 would be half power, not the same as half speed). Let’s just say bigger values make it go faster and smaller values make it go slower. If you send a spindle speed command which is greater than the value of $30 then $30 will be used instead, so setting a speed of S2500 followed by S1500 is translated into actual speeds of S1000 followed by S1000.

I don’t have the means to measure the spindle speed, this but others have. It seems to be roughly 8,500 RPM not under load!

NOTE: When using a Laser it is important that the value of the Max spindle speed matches any maximum power setting in your software. Earlier versions of Grbl only supported 0-255 as the laser power levels, so you may find your laser software has a max power value of 255. If you have $30 set at 1000 this will mean you are never allowing the laser to be set at more than ¼ power.

The minimum spindle speed. Zero is always treated as off and if the spindle speed is set below the minimum and is not zero the value of $31 will be used instead. I don’t think this really applies to the 3018 series of machines so leave it at 0.

$110, $111 and $112 – Maximum speed of movement on the Axis. These, set in mm/min, are the maximum speed the spindle or laser will move. If a command sent exceeds them the max value is substituted. Note that although the stepper motors and the threaded rod is the same for all the axes, which should give them the same movement rates, the rate of movement on the Z axis is often set lower. I think this is because if you are moving a bit down they don’t think it should go quite as fast. I can see no other reason why these should be different and they are MAX speeds, your CNC and CAM software should specify these values for the specific job you are doing.

$32 – Laser Mode
This is a Boolean value or on/off, 1 is on (laser connected), 0 is off (spindle connected). If you don’t have a Laser module then just leave this set to 0. If you do then I suggest downloading and reading Introduction to CNC for the Total Novice – Setting up a laser.

I strongly recommend setting Laser Mode On (1) when using the laser module.

I also very strongly recommend setting Laser Mode Off (0) when you use the machine as a router, moving a non rotating bit into a solid surface never produces anything other than nasty grinding noises and potentially damaged bits and stock.

## TRYING IT OUT

This is the bit you have probably been waiting for! I know I was.

Oops, still a couple of things to cover but are integral to the trying it out.

I still am unsure if this section should be at the end of this or here, on the one hand is the impatience of wanting to try something new for the first time which places it here! Or the patience to read the rest of the, possibly boring, information which would place it at the end. Impatience Wins!

### Mounting the Stock

Before letting the bit start spinning you will need some stock, a bit of something to cut. For the first attempt a piece of scrap wood is best, should be at least 10x10cm and over 4mm thick the sample files I provide will only cut to a depth of 1mm or so. What is important is that it is fairly flat and level. You could use other materials but a bit of wood is cheapest and simplest.

Your machine should have come with 4 clamps something like this.

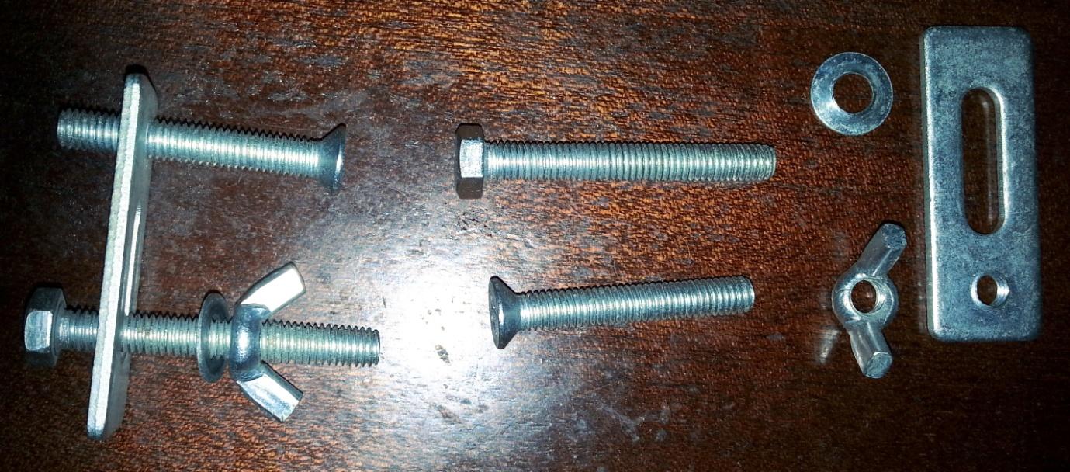
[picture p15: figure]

Put the pieces together so they transform into the one on the left. OK these are cheap, there are better ones out there but at extra cost, but these do the job!

The head of the bolt slides into one of the slots on the bed, the screw is used to move the plate to be approximately horizontal when the end of the screw is on the bed and the top of the plate is on the stock. The wing nut then tightens each plate onto the stock holding it firmly in place, the bolt will spin in the slot until it is reasonable tight so hold the top of the bolt while initially tightening the wingnut. Yes this is another of those ‘using your third hand’ jobs! It is best to use all 4 spaced around the stock, just one or perhaps two, will allow it to move, it depends on the depth of cut, bit you are using.... on how much force is exerted on the stock. If the stock moves during the job it is [Insert expletive here].

While clamping it down you need to make sure that the alignment of the stock on the bed is correct. Tricky to get it perfect at this stage as almost certainly your bed will be slightly out of alignment, not a lot but a little, as you are unlikely to be mounting and framing this first attempt it is close enough to use the edges and slots in the bed to be very close. Assuming that the scrap piece you are using is exactly rectangular of course!

There are other methods for holding down the stock, some of the common ones are;

- Double sided tape
- ‘Blue’ painters tape and superglue
- Gravity and friction (only applicable if you are using a laser)

### Mounting the bit

Normally you will have a set of bits provided with the machine. I believe SainSmart now includes an assortment of bits with their machines, but it used to be a number of identical engraving bits.

For this first cut I suggest you use an engraving bit.

The ER11 collet (not the holder) is 18mm deep. That is the clamping length, the bit will go into the collet much further if it is long enough, but only 18mm applies any clamping force which is fine. If the bit I am using is in total 38mm long, tip to toe, it will leave 20mm sticking out of the bottom of the collet when fully clamped. You don’t want to leave too much sticking out as this will create a greater leverage from the end of the bit which can lead to it flexing or breaking (especially true for small diameter bits) and putting greater strain on the router. But you also don’t want to leave too little sticking out, it needs to be able to reach the bottom of a cut without bouncing off the limit at the bottom of the Z axis, and be capable of cutting down far enough for whatever you are doing.

Slide the bit into the collet and use the two spanners provided to tighten it up.

### Positioning the bit

I mean moving it to the starting position on the X, Y and Z axes and telling the router ‘Start from here’. The router has to know where you want it to start before you start it, otherwise it will just assume things and almost certainly get it wrong!

Part of getting the start position right is being aware of the size of the job you are going to start and where the .nc file expects to start from. The visualisation in candle and similar software when you load the .nc file can be very useful to work this out.

So make sure the end of the bit is clear of the top of the stock and move it using the jog controls to where you want it to start. Keeping the end of the bit close but not touching the stock makes this easier to see. Fairly easy when using a V or engraving bit as it has a pointy end which you should be able to see quite clearly, not quite so easy when you use a larger flat bit or if your stock does not have clearly defined corners as you can’t see the centre of the bit or the corner of the stock.

So I have devised the Bit Positioning aid to assist. (See accompanying files)

Simple in concept, it’s just a series of circles where the diameters have been chosen to match my selection of bits and any I may acquire in the future (13, 8, 5, 3.2, 1.5mm) with 2 lines across them. It’s not the sizes that are that important, it’s just by rotating a larger bit I find it easier to align it to, or in the centre of, a circle. These are a compromise, make your own, scale it, it doesn’t matter.

To place on a corner apply a bit of glue or cheap double sided tape, I say cheap as I only want it to stick for long enough to align the bit and not leave any glue residue on the stock.

To position on an edge align the cross lines up with the edges of the stock and stick it down. It is often easier to use a ruler or straight edge on the sides of the stock to assist.

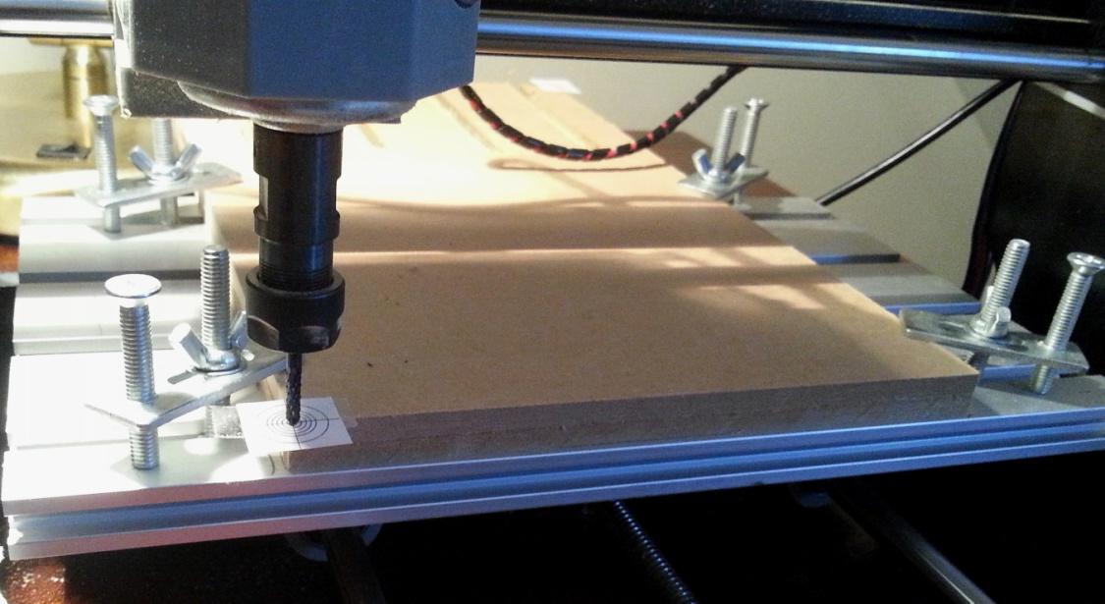
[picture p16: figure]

These can also be used where the edge of the stock has been rounded using the same technique, if so and the centre is not supported by the stock don’t use it to set the Z axis position!

To position anywhere else, well.....

Remember you can turn the bit by hand during the alignment process to make it easier to see.

Print them out, cut them up and see if they work for you. They can be attached anywhere on your stock and removed as you see fit. Depending on what you are doing these may be totally useless! It depends on how accurate you need to be with your setup, if you are going to cut off the edges of the stock anyway then there is no need to be other than close. But if you are going to turn the stock over and machine the other side as well, this MAY make it more accurate and easier, It’s never going to be 100% accurate!

So now the bit is aligned in the X and Y axes.

Now the Z axis, Candle allows, nay requires, that the zero position of the X and Y axes and the Z axis are set separately. Not that silly as it allows you flexibility. You don’t have to set the Z position in the same place as the XY.

Setting the exact position of the Z axis zero is just as tricky as setting the XY axes position! But different. Start with the end of the bit close to the stock by eye then slowly jog the spindle down (0.1mm at a time or less) while turning the bit by hand until you encounter resistance from it touching. The problem with this is that it can mark the stock and if you are using a small bit, especially an engraving bit with a sharp pointy end it can be difficult to detect the resistance.

So place a piece of thin, Paper is excellent, material between the stock and the bit, this stops any scratching and by trying to move the material sideways you can tell when you encounter resistance to movement that it is starting to touch. Then remove the material and jog down by the thickness of the material before you set the Z Axis zero.

HINT: Make a stack of the paper until you can accurately measure the thickness of the stack, then divide by the number of sheets in the stack to get the thickness of each sheet, the thicker the stack the more accurate your results will be, it’s more reliable to measure the thickness of a large number of sheets (without a micrometer) and divide it down than it is to measure 1 by itself!

I normally use one of my printed bit positioning aids, with the card I have printed them on I know the thickness is very near to 0.25mm (I measured a stack of 20 at about 5mm).

### Pressing the Buttons

So Jog to the XY axes origin, in Candle click the Zero XY button in the Control section.
Now position the end of the bit to just touch the stock and click the Zero Z button in the Control section. The Work Coordinate System origin is now fully set.

I recommend at this point using the jog buttons to retract the end of the bit to a safe distance (a few mm) from the top of the stock. This hopefully prevents the GCode file from dragging the bit across the top of the stock as it goes to the first cutting position. Not all GCode files will do this, some will, it all depends on the software used to generate it and the options used.

Fit the bit, a 20 degree engraving bit

Load your sample file in Candle. SainSmart provides these on the mini CD which came with your router. If you can’t read the CD then you can download everything from http://wiki.SainSmart.com/index.php/101-60-280PRO A good start is 1SainSmart.nc, this is designed to use a 20 degree engraving bit.

dragon.nc is also good but takes a while to complete, just because it is a complex engraving, also uses a 20 degree V bit. In fact it is a good initial ‘stress’ test for your router, and it’s pretty!

Look at the visualisation in Candle carefully, especially the dimensions and where the origin is, make sure this matches the size, position and alignment of your stock.

Make sure Candle and the router are connected.

Click Send.

NOTE: It is possible that there may be some errors reported, even some of the (earlier?) SainSmart sample files generate errors. The most common one is an unrecognised command (error:1) Normally the error 1 can be safely ignored, it commonly consists of including a % or Txxx command in the GCode - % is an old start of program and do not rewind the paper tape when finished command. T commands mean change the tool. As the router does not have a paper tape reader or a tool carousel it does not recognise these commands.

## Hopefully Congratulations, it works! If not review and repeat!

NOTE: I forgot to say have a vacuum cleaner ready to clean up the debris!

## Some background and terms – (In no particular order)

Skip this if you want, it is not necessary but if you ask for help on forums you may see these terms and concepts used and if you don’t know them then it may be useful.

### Units

Pretty obvious but can cause a load of problems. Basically these will be in inches or mm, there are other variations for speeds such as mm/sec and mm/min . The software you will use to create things will have its own settings, some even will work in Inches! It is imperative that the units match, if you tell your software to work in Inches and the router works in mm you are going to get very compressed results and vice versa, move left 1 is very different in mm and inches!

### Controller or Motherboard

This is the bit of electronics which controls the movement of the bit or laser and the rotation speed or laser power. On my 3018-PRO this was the Camtool 3.3 board and is now the Woodpecker CamxTool 3.4, whose brain is an Arduino microprocessor. It’s not a very big brain but works well. The Arduino microprocessor system is often used by hobbyists and for microcontrollers in situations like this. Lots of other makes, versions and types are available.

The motherboard also has all the electronics needed to drive the stepper motors which control the axis movement, to drive the spindle motor at differing speeds and the laser at different power settings, translate GCode commands received via USB or an offline controller into specific motions of the laser or spindle and receive and process other commands, for example for jogging (moving) the spindle around, changing settings, returning status etc.

Grbl
This is the software which runs on the motherboard; it basically takes GCode and translates it into the movements and speeds needed to for example cut a line. Grbl is free to use open source software.

When Simen Svale Skogsrud first sat down and wrote Grbl in 2009, he named it after a bigger version of a computer mouse. It's small, useful, and doesn't do much other than what it’s designed to do. So, if you ask him, it's pronounced like "gerbil".

Mach3
If you have the MX3 or similar models these run the Mach3 software. I have never used it.

### Stepper Motor

A motor that is told to turn in small steps like turn clockwise 1.8˚ as opposed to a ‘normal’ motor that will try and continue to rotate as long as power is supplied.

All of these routers use stepper motors to control the movement of the axes; each step of the motor will turn the threaded rod a bit, which will move the things connected to it by a small amount. The amount the axes move depends on the stepper motor, the pitch of the threaded rod, the motor controller and the router motherboard.

Microsteps
Where the stepper motor is told to turn by a fraction of its rated step by application of fractional electromagnetic forces (OK Magic!). This depends on the motor and the motor driver chip used on the motherboard, one microstep determines the minimum movement or precision of the axes, this also depends on the pitch of the threaded screws.

Missed Steps
You may often see this as a possible cause of errors, quite simply it’s when the stepper motor is told to move, but for whatever reason doesn’t. The causes can be varied, asking it to do too much is the simplest, this can be because the bit is cutting deep and has now been told to move sideways putting too large a load on the stepper motor, or the machine is at the edge of its limits and that step will bang it into them, or bad wiring, or.....

But the motherboard is calculating the position of the spindle based on what it has told the stepper motors to do, it doesn’t know if they have actually done them. If the motor doesn’t move the spindle then that position is now in error. Missed steps will always cause the router to become misaligned. They can often be identified by misaligned cutting or by nasty grinding noises coming out of the router.

### PWM (Or TTL)

Pulse Width Modulation, which is often implemented by Transistor to Transistor Logic (TTL). You may see either on any control board connector, but practically they are the same.

Simply put its turning something on and off very rapidly (up to 1,000 times per second). Imagine you didn’t have a dimmer switch on a light but wanted it to operate at ½ brightness. Simple, stand by the switch and repeatedly turn it on and off where it is on for 50% of the time and off for 50% of the time. OK not recommended, it will probably give you a headache, but if you use a computer or electronics to do this 1,000 times a second all you will see is the light burning at 50% brightness. Change it so it is on 75% of the time and it will be brighter, less and it will be dimmer.

### Spindle Motor

This is the ‘big’ ‘normal’ electric motor which holds the cutting bit. The power it is supplied can be varied changing the speed of rotation, the rotation speed also depends on the amount of work it is being asked to do, just like driving a car at a steady speed on the flat, starting to go up a hill the car will start to slow down as the engine is having to do more work.

The motherboard uses PWM to vary the speed but provides no feedback to measure the speed. So it’s more of a power setting. Normally it is set as a maximum speed of 1000 even though the RPM of the standard Spindle motor will be higher, the best I can find for the true speed is about 8,500RPM under no load at the 24V supplied by the router motherboard.

This value is not going to be linear, in other words a speed of 500 will not be exactly half the RPM of a speed of 1000.

### Bed

Not for sleeping, this is the flat aluminium bit which holds the stock with slots in it to allow clamps to hold the stock down.

### Tool Holder

Simply this is the piece that fits onto the end of the spindle and holds the bit, the chuck on a drill.

ER11 Tool holder
The commonest tool holder on this type of machine, it is manual requiring a couple of spanners to release and fasten it by tightening or releasing the collet which clamps the tool.

Collet
The piece inside the tool holder which as it is tightened into a tapered hole contracts around the bit so holding it.

This only tightens so far, a collet has a limited range of movement around the bit, but the diameter of the hole in the centre determines the range of bit sizes it can clamp. The standard collet supplied with mine can take a bit with a shank of around 3.175mm (or 1/8”). Other collets are available! I have the SainSmart collet set which allows me to use bits with a shank diameter of 1 to 7mm NOTE: a bit with a ¼” shank diameter fits into the 6mm collet.

HINT: If you need to change the collet unscrew the end cap from the end of the tool holder, this will leave you with the collet inside the end cap, it snaps in. Now push the end of the collet as far as you can over to the side of the end cap tilting it. Using your third hand press something flat like the end of a spanner onto the collet to break the snap in effect and push it out.

### Bit (or Tool) Introduction

The sharp, sometimes flat, often pointy thing which rotates and cuts bits out of the stock.

So many to choose from, so you know what you are buying. Remember this is a bottom end machine, larger routers with much higher powered motors can happily drive the larger bits and will routinely do so, however at this level if you try and use a 50mm diameter bit then these routers probably won’t be able to turn it when it starts to cut, certainly not at the speeds it was designed for. See a later section on bits.

### Stock

Whatever you are trying to engrave, cut or carve.

### Tabs

Not credit in a bar!

If you for example are cutting out a shape then when you get towards the end of the cut there is nothing holding in the centre. Fine if you have fixed it down, if not then it will start to move as the last bit of material is removed. This is commonly known as a disaster! It will collide with the edge of the stock cutout and the bit damaging the edges and if it wedges in the wrong place potentially breaking the bit!

Tabs are where you set in the model a number of small bits of material which should NOT be cut out to hold a centre piece in position, It’s like a coarse perforation round the edges of stamps! These have to be removed manually when the cut is finished.

### Tiling

A technique for making things larger than your router. The gantry of the router effectively limits the width of the stock to 300mm, however there is nothing to stop it from sticking out of the front and back, but you are only going to be able to cut or engrave a maximum of 180mm at a time. But after doing the first bit you can move the stock up or down and cut or engrave the next 180mm. The problem is being able to align the 2 or more ‘tiles’ exactly.

### Spoilboard/ Baseboard / Wasteboard

A bit of sacrificial material mounted on top of the bed and underneath the stock which can be levelled exactly. Baseboard, Wasteboard and Spoilboard are just synonyms. Here I will use Spoilboard.

Why use one, there are a number of reasons.

If you are trying to cut completely through the stock creating a stencil with the laser or cutting out a piece from the stock without a Spoilboard of some sort you are going to start cutting the nice shiny Aluminium Bed. And if for example you are using a router bit to cut through wood it is suddenly going to make contact with a piece of Aluminium which is a lot harder and it probably won’t like it. It will get blunted and possibly break to say nothing of what it will do to the bed!

It is important that the bit (or laser movement) is absolutely parallel to the surface of the stock. Imagine if the right hand side was 1mm lower than the left. If engraving for example this would probably mean that if you started on the left by the time you got to the right the bit may not even be touching the surface. If routing or carving your cuts may be too deep or shallow.

Using a Spoilboard mounted permanently and securely means you can use a bit to slightly level or face the surface which makes the top level with the movement of the bit. Even if the level of the bed is slightly out which it almost certainly will be, after facing it the top of the Spoilboard will not be, as long as it is securely mounted and is not moved. If the level of the bed is out by 0.2mm on the X axis this gives an angle of roughly 0.03 degrees so put away the spirit level!

As a last step I engrave my Spoilboard with a grid. These lines are exactly parallel with the actual movement of the bit or laser which makes aligning the stock to the actual movement, even if the bed itself is a little skewed which it will be, much easier.

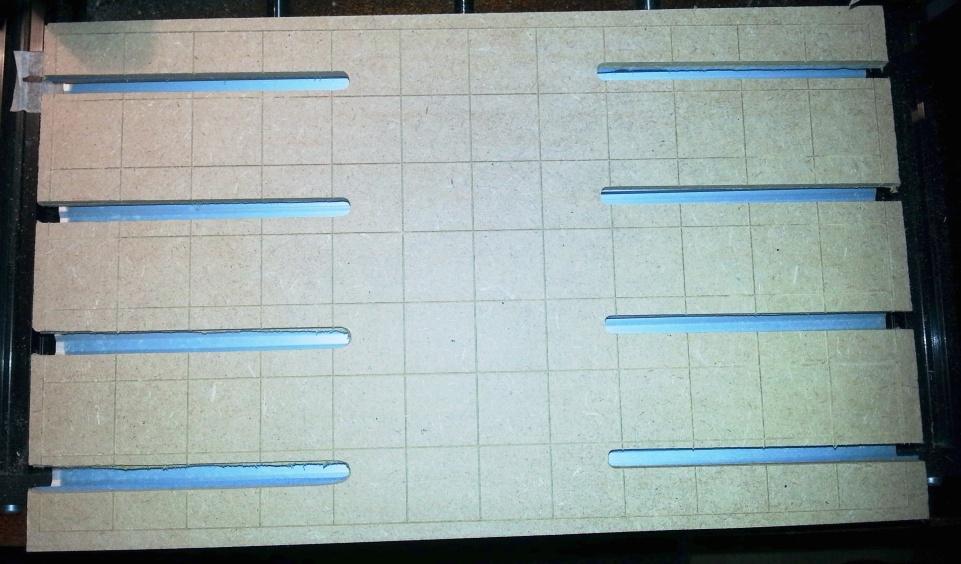
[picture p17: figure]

It’s a new machine with a clean and shiny aluminium bed, so let’s keep it that way.

It’s really all that simple. (Coughing fit!)

Lots of room for experimentation here!!!. See “Introduction to CNC for a Total Novice – Making a Spoilboard.”

### GCode

Geometric Code (I think) is a set of simple and some more complex commands which basically work out to go to there, up a bit, down a bit, left a bit, spin faster.......

The router motherboard reads these commands one by one and translates them into the commands sent to the stepper motors driving the axes and the spindle motor or laser. So to get the router to do anything it needs a series of GCode commands, as that is what it understands, it uses those commands to control the movement of the bit in all the axes at the appropriate speed.

GCode is normally saved with a .nc file extension, although other file extensions are used, it’s just a text file which can be opened in any text editor or viewer. So if your CAM software generates XXX.GCode and your GCode sender only reads .nc files just rename it. Some software will connect directly to the router and just send it the commands rather than saving a GCode file and letting something else send it to the router.

GCode dates back to the 1950’s and to be quite honest it is not a standard, well there are lots of standards. In the words of Barbossa The code is more what you'd call "guidelines" than actual rules. Welcome aboard the Black Pearl, Miss Turner!

Every CNC manufacturer ignores bits which they don’t implement, like the tool commands which say go and pick up tool x from the automatic tool carousel, the 3018 doesn’t have a tool carousel so it generates an unknown command error on a Tool change command even though the GCode is valid. Manufacturers often add extensions to support the unique features of their machines.

List of Supported G-Codes in Grbl v1.1:

- Non-Modal Commands: | G4, G10L2, G10L20, G28, G30, G28.1, G30.1, G53, G92, G92.1
- Motion Modes: | G0, G1, G2, G3, G38.2, G38.3, G38.4, G38.5, G80
- Feed Rate Modes: | G93, G94
- Unit Modes: | G20, G21
- Distance Modes: | G90, G91
- Arc IJK Distance Modes: | G91.1
- Plane Select Modes: | G17, G18, G19
- Tool Length Offset Modes: | G43.1, G49
- Cutter Compensation Modes: | G40
- Coordinate System Modes: | G54, G55, G56, G57, G58, G59
- Control Modes: | G61
- Program Flow: | M0, M1, M2, M30*
- Coolant Control: | M7*, M8, M9
- Spindle Control: | M3, M4, M5
- Valid Non-Command Words: | F, I, J, K, L, N, P, R, S, T, X, Y, Z

If it’s not in the list above (taken from the Grbl 1.1 release notes) it will be unrecognised and an error will be returned from the router, these invalid command errors (error:1) can normally be safely ignored.

GCode can even be generated by hand as it was in its early days. For example

S100
M3
G91
G1 Z-0.1
G1 X10 Y10
G1 Z0.1
M5
Means Set the Spindle speed to 100RPM, Turn the spindle motor on in a clockwise direction (Or laser On), Use relative positioning – each movement specifies an offset from the LAST position, Move the bit 0.1mm towards the bed, Move the bit 10mm to the right and 10mm up as a linear move, move the bit away from the bed by 0.1mm, turn the spindle off.

But as nowadays we have these newfangled things called ‘Computers’ for anything other than the simplest of jobs, coding this by hand this would be exceedingly tedious, there is a reason computers were invented.

So practically to generate anything much more complex in a GCode file we need software. But that unfortunately creates its own set of problems. Commercial stuff is built for precision and speed and as GCode isn’t really a standard but a set of them manufacturers are relatively free to add features, interpret things in slightly different ways.... So the CAD/CAM software has to generate the GCode specifically with each specific machine in mind. Even in the hobby world there are differences, the easiest one is does your router have limit switches which allows it to set a machine position, is it mounting a spindle motor and bit or a laser, and how powerful is it?

There are lots of GCode tutorials out there so I am not going to even attempt to duplicate them, but beware of how machine specific they are, although the general principles will be the same.

I have found however that it is useful to have at least a basic understanding especially of positioning and coordinate systems to try and work out what has gone wrong. Don’t blame the router it’s a fairly dumb machine which tries to do exactly what it is told!

### Toolpath

Simples, the path that the tool is moved along in order to do the job. This is normally expressed by the software analysing the model, using the information you have told it about the tool, how fast to move it etc...... and generating a GCode file which tells the router what to do in little pieces. Up a bit, down a bit, left a bit....... Often your software will provide a toolpath simulation so you can see on your computer what is going to happen before you send it to the router.

WARNING: These simulations always seem to ignore the getting the bit to the start of the cutting and returning it somewhere at the end. That’s because they don’t know where your bit or laser is going to be when you start the job.

### Limit Switches or End Stops

Switches which trigger at the limits of movement for each axis. Used to allow the router to establish a ‘Home’ position by moving around until they are triggered. In operation they will stop the router from trying to move past its physical limits by generating an alarm. Not fitted to the 3018-PRO.

Soft Limits
This can only be used when a home position can be set via a homing cycle. It allows you to use 3 limit switches to detect the left, front and top limits, all that is needed to set a home position, rather than fitting 6 to also determine right, back and down limits.

Soft limits set the maximum travel from the home position, the router software checks if a
movement will exceed the machine limits and raise an alarm if it will, just as it would if a limit switch was activated.

### Coordinate systems

When you turn on your router it has no idea where it is on any of the axes, it doesn’t save its position and even if it did you could have manually changed them. All it knows is ‘I am here!’ Pretty much like me waking up in the mornings.

One thing to remember, these are hobby machines, the main drive, at least until recently, for the development of CNC is commercial manufacturing. If you are expecting to spend £250 on a router you cannot really expect the same construction, tolerances and features you would get if you were spending £25,000 on the machine.

You need to know three things and how they relate to each other to stop your machine scraping the bit over the top of your stock, suddenly deciding to plunge down as far as it can or banging against the physical limits of the machine:

1. Home or Machine coordinates
2. Safe Position
3. Work Coordinate System

Home/Machine coordinates
The Home position is where the spindle is when you turn it on! This position is remembered as the home or machine origin position, not a lot of use, but higher end machines have these devices called limit switches which tell it when it has reached the limits of travel. This allows the use of a homing cycle where it moves to test when the switches activate so telling it where a ‘Home’ position is. This is normally the spindle being at the bottom left corner and as high up as it can go.

This position cannot be set via commands to the router other than telling it to perform a homing cycle. Well it can, but only by jogging somewhere close to it and then powering the router off and on or resetting it, it sets its power on position as home.

Safe Position
I always had a safe place where the monsters were unable to reach me. Well routers are the same, have you stroked yours lately and told it that at least you like it??

Often Software will generate GCode using the G28 series of commands which specifies a ‘safe’ position to which it should return to. This is RELATIVE to the home position and it is remembered by the router. By default , unless the router receives a G28.1 command, which is set the safe position, it will be an offset of 0 on all axes from the Home position, so if you don’t have a consistent ‘home’ position it can rapidly become an ‘unsafe’ position!!!

Going 20mm up, 90mm right and 5mm forwards when you don’t know where you started from is not a good idea!

Certainly Fusion 360 generates the GCode with moves to the ‘safe’ position on by default, but you can turn it off in the Grbl post processor options, turn G28 Safe retracts off.

Imagine the following circumstances:

- When you turn the machine on the end of the bit is 1mm above the top of the Spoilboard.
- Jog the bit out of the way.
- You mount some stock, lets say 5mm thick using clamps on the Spoilboard.
- You run a milling job.

At the start the code tries to send the bit to the home or safe retract position, normally first moving to the Z axis safe position then to the XY axes safe position in a straight line. At the end of the job the bit is returned to the home position the same way.

PROBLEM! The clamps and what remains of the stock are probably in the way, this can be disastrous as it tries to smash its way through things. Sometimes you will see people reporting that at the end, sometimes the start, of a job that the bit is dragged across or through the surface marring the stock or starts by plunging straight down. This is the probable reason why.

Work Coordinate System (WCS) Sometimes referred to as Local Coordinates. This is what you will be using for every job!

Most machines including GRBL ones support multiple origins. This is so if you want to make multiple parts at the same time you can set up multiple origins then say use Origin 1 – Make the part, use Origin2 – Make the part..... Apart from letting you know about it I am now going to ignore it.

This is basically setting a position for the start of the work, or work origin. Even if your machine knows its home position it’s still going to base an operation on WCS as it’s easier to position the bit or laser to the bottom left, touching the surface of the stock than it is to mount the stock exactly according to the home position.

In other words jog the bit or laser to where you want to start the work, tell the router this is the WCS zero position and go from there.

It is your responsibility to make sure that you are not going to tell it to go outside its physical limits.

It is also your responsibility to make sure that the router can get to the start position without damaging anything, for example don’t leave the bit below or exactly on the surface of the stock! The first command sent to the router may well be to go to the WCS Origin or wherever the toolpath starts. This will be in a straight line so if there is something in the way?

CAUTION: Your Software will normally allow you to set a home position on your work before generating the GCode, Fusion360 is an example of this, you can set the origin of the work coordinates to bottom left, top right or anywhere else you chose normally relative to the stock. Top Bottom Left seems to be the most common but beware! If they don’t match the physical environment, stock position, starting position etc. of your router then there will be problems ahead.

Jogging to the start position is NOT enough depending on the software you are using, you must also register this as the starting position. Or your router may first go to where it thinks the start position is before starting. Within the Work Coordinate System (WCS) there will be a few buttons you can press on your PC. One will be to set the current position as the origin, In Candle this is the Zero XY and Zero Z buttons, in LaserGRBL this is the globe along the bottom of the screen.

It reminds me of a very old joke where a stranger is asking for directions, one guy looks and says that is difficult, if I was going there I wouldn’t set out from here, I would go to the next village first!

Examples
Firstly why am I spending so much time on this? Well it’s important and took me quite a while to fully (used in its loosest sense, sort of may be closer) understand what was going on.

NOTE: These are simplistic, just designed for illustration; real life is a lot more complex!

Take the following:

- Turn the machine on with the bit in the top front left corner, this becomes the home position. Or more likely turn it on, jog the bit to the top front left corner and then reset it.
- Mount the stock.
- Move the bit to the WCS origin using Jogging commands.
- Set the XY and Z axes WCS zero point.
- Jog the bit a little out of the way (optional).

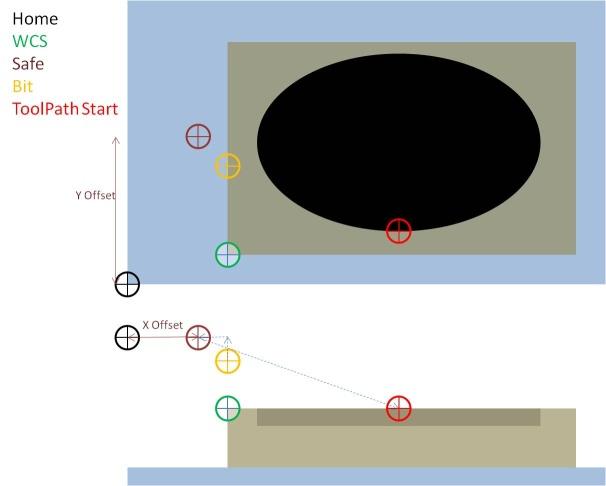
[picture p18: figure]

Now when you send a job to cut out the stock often the program generating the GCode will first move the bit to the Safe position normally Z axis first, often only the Z axis because that is safe. Then go to the start of the toolpath to start cutting. Everything fine!

But what if?

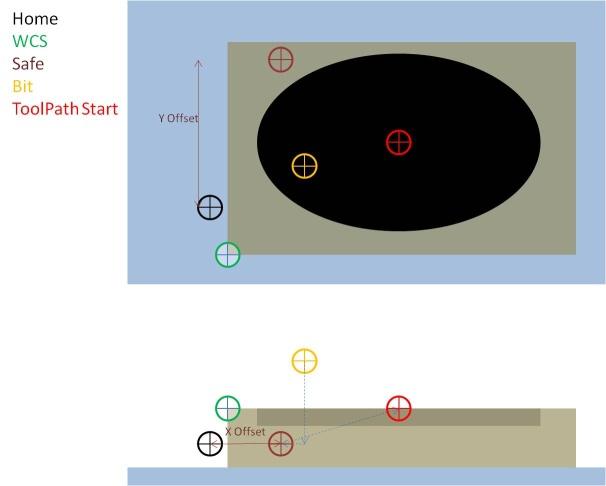
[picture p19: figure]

When you turned the machine on the end of the bit was close to the bed

OOPS! Going to the safe position is not safe, remember it is based on where the spindle was when you turned the router on, it’s actually in the middle of the stock! So expect the bit to try and plunge down into the stock before going to the toolpath starting point for the cut almost certainly in a straight line. After the job if it tries to return to the safe ‘Home’ position, then another Oops!

Even if it just says go to the start of the toolpath depending on where the bit is that may not be safe, if it was left at WCS origin then it will scrape its way across the stock to get there!

Here is the start of some GCode to cut a pocket generated from Fusion 360

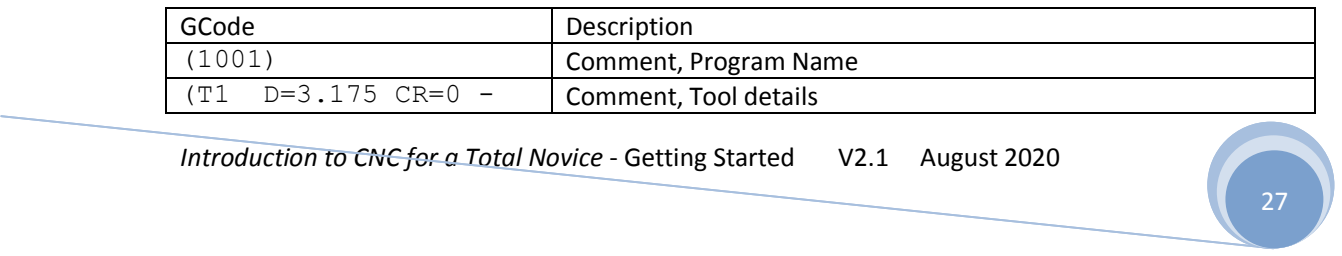
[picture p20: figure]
GCode; Description; Comment, Program Name; Comment, Tool details

ZMIN=-2 - flat end mill)

G90 G94 | Use Absolute positioning, Set federate units as X/mm/minute
G17 | Set the plane as X/Y
G21 | Set Length units in mm
G28 G91 Z0 | Rapidly go to the relative(G91) position of the Z axis as saved in the router. G91 mode is NOT saved. If G28 safe retracts is set to ‘No’ this line is omitted but everything else stays the same.
(2D Pocket1) | Comment, start of operation
S1000 M3 | Spindle speed 1000 and turn it on rotating clockwise.
G54 | Select Work Coordinate System 1
G0 X94.583 Y58.394 | Rapid move to the X and Y coordinates from WCS Origin
Z10 | Move Z axis to 10mm above WCS origin
Z5 | Move Z axis to 5mm above WCS origin
G1 Z2.817 F500 | Cut down 2.817mm from WCS Z origin setting a feedrate of 500mm/min.

### Absolute vs Relative Coordinates

The router will use either relative (G91) or absolute (G90) coordinates depending on the last one of these instructions it received. Relative means go 5mm to the right of where it is now, absolute means go 5mm right from the Home position or Work coordinate system origin depending on the command and current modes.

### Jogging

Don’t worry, in CNC terms this can be performed while sitting down and does not involve any physical activity other than moving a finger, maybe a hand as well!

This is a term used for manually moving the spindle around using buttons on the computer. These move the spindle around by varying, settable, amounts and are normally used to move to the Origin needed to start a job, or to move the bed to the front and the spindle out of the way to give easier access to set up a job.

NOTE: If using jogging to move to the origin of a WCS then putting it in place is not enough, you will also have to specifically tell the router that this is where you want to start from by zeroing all the axes.

### Stock

The stock is the term for whatever you are cutting, engraving, milling, whatever.

Different materials have different characteristics. You need to understand and experiment, which I am looking forward to.

This router is, “Capable of cutting all types of plastics, soft aluminium, woods, acrylics, PVCs, and PCBs, the Genmitsu can be used on a wide range of projects and materials.”

But there are large differences in the details, the harder the material the more difficult it is to cut!

### Feed

The rate/speed which the bit or laser is moved through or over the stock (Fxxx); this is controlled by the axes stepper motors. This is normally expressed as mm/min, and that is what the 3018-PRO uses by default for feed rates.
There are many other ways of measuring the feed rate, some depend on the bit you are using to try and calculate how much each cutting edge is cutting out of the stock. This is normally best left to the professionals for the moment.

### Speed

The speed of rotation of the spindle(Sxxx), for a laser the power it operates at. Remember the 3018-PRO has no measurement of the actual spindle speed or power, so mostly this works out to be faster and slower. As such if you try and do too much the spindle will slow down... In a much more expensive machine a spindle speed of 500 would probably mean 500 RPM.

Simple, but....

Feed and Speed are somewhat dependant on each other, the goal is to achieve the cleanest possible cut hopefully in the fastest possible time with no wear on the tool, although as a hobbyist the time can be less important than to a professional.

Also to be taken into account is the stock material and the depth of cut you are trying to make.

Think of it as the amount of material you are trying to remove in one go. The faster you set the feed the more the cutter will travel on each revolution making for a thicker cut, the faster the spindle speed the amount each rotation of the bit has to remove is lower.

### Passes

This is basically the number of times you tell the router to retrace the same path, probably with a bit of go down between each pass.

If you want to cut a groove or pocket in a piece of wood 5mm deep you are not going to do it in one single, go down 5mm then cut! If the wood is very soft and the bit is very sharp, maybe, but you take the risk of overloading the router, wearing out or breaking the bit by trying to make it do too much work in one go.

You can get round this by telling your CAM software to make multiple passes cutting out a little each time. As a general rule the less material you take out the better the finish quality but the longer it takes.

This also depends on the hardness of the material, you would need more passes using smaller cuts on oak than you would on a soft pine. Take notes so next time you have a better idea where to start!

### Z-Probe

NOTE: Before discussing Probing or Z-Probes in public make sure that the people within listening distance are all into CNC Routing. Otherwise they will either think you are an Alien in disguise or have just been returned after your abduction.

A Z-Probe is a simple device, it’s a piece of conductive material with a wire attached (Or a spring loaded switch). Another wire is connected to the router and clipped to the bit in the spindle motor. (it’s a switch) Very simplistically the bit is lowered onto the stock until contact is made. This tells the router where the origin of the Z axis should be.

I haven’t got one!

Lots of different ideas and suggestions on the Internet and forums.

### Height Map

This (if your software supports it) is using a Z-Probe repeatedly over the stock to build up a map of the heights. Often used when engraving Printed Circuit Boards where the vertical tolerances required to engrave the PCB correctly are very fine. When engraving the software uses the map to adjust the Z axis to correct the actual height of the bit relative to the stock depending on the XY position.

### Vref

The router motherboard contains motor drivers for each of the stepper motors. Depending on the stepper motors you have the maximum amount of current each driver can supply is controlled by a Voltage reference or Vref which is set by turning a small trimmer pot on each motor driver. This can be adjusted by turning the trimmer pot using a very small screwdriver and measuring the voltage from the pot to ground. The exact setting depends on the stepper motor and the motor driver chip. Too high and the driver will try and provide too much current and probably burn out. Too low and the stepper motor won’t get enough current and could miss steps. If your supplier has good customer support it is likely that they have taken some care to get this right as to be honest it costs money to replace motherboards. If not it could be worthwhile checking, also if you replace the motherboard which may not be set up for your exact machine.

Search the Facebook SainSmart Genmitsu CNC Users Group for vref, my thanks to Steve Harhai.

### Offline Controller

This is a small module with an SD card which connects directly to the router Motherboard. It can read a GCode file from the SD card and send it to the router. A bit limited in what it can do but very useful if your PC is too far away from the router or you don’t want to tie it up for the duration of a longer job. NOTE: You cannot connect the offline controller and a USB to the router at the same time! They use the same serial interface on the router and it will get very confused! Also the offline controller has a USB interface which allows it’s SD card to be used by the PC as a drive. Don’t use this while the Offline Controller is talking to the router!

## The Process

Before you start doing anything it helps to understand the process you are using

Starting at the Router and working backwards.

The router understands a set of commands called GCode. Plus some other management bits and pieces. It receives these over a serial communications link, normally from a PC or other device such as an offline controller.

### Talking to the router

The bottom layer is the bit you need to send the GCode to the router. At the end of the day ‘all’ you need is something that will send a text (GCode) file to the router.

However some clever people have taken this and added some useful bells and whistles. The 3018-PRO uses the Grbl program on its motherboard. So if on your PC you use Candle/Grbl they will talk to each other quite happily (as will others). Candle also adds some other useful features such as allowing you to move the router bit around, set zero position, see what is happening etc.....

If you are using the laser module LaserGrbl does much the same but is more set up for using a laser.

There are also things like Offline controllers which can read the .nc file off an SD card and send it to the router without it having to be connected to your PC.

There are lots of other possibilities but for the 3018-PRO you will be using Grbl based systems.

### CAM (Computer Aided Manufacturing) Process

Basically this takes a model, be it a picture, 2D or 3D model and determines how the tool needs to be moved in order to create the GCode necessary for the router to carve or engrave the part out of the stock material. This is called generating the toolpath which is then converted to GCode.

In order to do this it needs to be told things like what tool it is using. This can make a big difference if you are using someone else’s GCode file! If they built the GCode to use a 20˚ engraving bit and you are using a 3mm routing bit or vice versa the results are not going to be good! Also you are not going to be able to carve or drill a 2.5mm hole using a 3mm bit. And if you are trying to carve aluminium rather than soft pine you will certainly need to tell the router to use a slower feed rate to move the bit and a different spindle speed.....

The CAM software will almost certainly allow you to specify things like the number of passes to make, how much the bit should be lowered between each pass etc.......

### CAD (Computer Aided Design) Process

This is defining what you want without having to, at this stage to specify how to make it. This could be a 2D graphics processor (engraving Jpegs) up to a full 3D modelling system. The output of this is fed into the CAM process.

Unfortunately this does not mean you can totally ignore the manufacturing process even when designing things, you are not going to be able to make a 90 degree internal corner when using round router bits, you will have to add a fillet (radius on a corner) size suitable for the router bits you have and intend to use.

### Welcome to The Real World!

The boundaries of the process model can get very blurred by what you are trying to do and the software you are using.

For example I am learning Fusion360 as a CAD/CAM tool, not only does it provide all the CAD functionality it also has a Manufacture mode where it does all the CAM work generating the toolpath and creates the GCode file to be sent to the router.

Candle, which mainly is the talks to the router bit, can also load graphics files and generate the GCode before it sends it to the router without saving a GCode file, this is CAM as well as talking to the router.

It’s all really simple (Cough, Cough)!!!!

But regardless of the software you choose to use the process is the same, it’s just that different software developers have chosen to implement different parts of the process model.

## Bits in more detail

So you have the router, a piece of wood or something and want to make something, you are going to need a bit to put at the end of the spindle.

There are lots and lots and lots of choices here, hundreds, nay thousands, nay hundreds of thousands!

Bear in mind that most of them are designed to be used on much more powerful machines and that as standard your router almost certainly comes with a collet which will take a 3.175mm (1/8”) shank.

First some terminology (NOTE: As always there are lots of names in existence for the same thing).

Term | Description
Collet | The part of the tool holder that squeezes tightly on the bit to hold it in place. The size of this must match the shank size of bit you are using.
Shank or Shaft | The part that goes into the collet of the tool holder
Shank Dia | The diameter of the Shank, this must match the size of collet you are using or it either won’t fit or you won’t be able to tighten it enough to hold it in place.
Shank Length | The length of the shank, before it turns into a cutting surface, which can fit into the tool holder’s collet.
Stickout | The distance the bit sticks out from the bottom of the tool holder collet, this is used by some speed and feed calculators.
Flute | A cutting edge at the end of the bit.
Flute Length | The length the cutting surface extends up the side of the bit. This would be the maximum depth you can cut in one go. This is practically far, far more than the bit can cut at any one time.
Flute Count | The number of cutting edges at the bottom of the bit. A 1 flute bit will take a chunk out of the stock every rotation, 2 flutes means every ½ rotation...... More tends to give a finer finish, but only at a slower feed rate. (I think)
Overall length | Total length of the bit tip to toe.
Shoulder length | The length of the bit from the tip before it becomes wider than the cutting diameter. If the diameter is less than the shank diameter this is the maximum depth it can go into the stock regardless of any number of cutting passes.

Diameter | The diameter of the cutting tip and/or flute, the size of the hole it will make.

The 3018-PRO has an ER-11 collet holder at the end of the spindle motor. As standard this is supplied with a 3.175mm (1/8”) collet. Upgrades are available, search for ER-11 collet, SainSmart also sell a set which covers 1mm to 7mm shank Diameters.

NOTE: Lots of bits you may see advertised are for much more powerful routers, While the 3018-PRO is not a 1 Stone weakling (well actually in CNC terms it is), neither is it Charles Atlas. The larger the diameter of the cutting surface the more power it takes to turn it and drag it through the material.

### Bit Types

This is a very brief discussion of some of the various bit types and is NOT all inclusive.

Name | Description
V|V Groove|Engraving | V says most of it, the cutting tip is a V shape with the sides of the V being at various angles to each other. Believe it or not this will cut a V shaped groove in the stock.
End Mill|Router | These are designed to cut straight groves in the stock. There are lots of variants.
Surfacing |Fly Cutter|Spoilboard | Surfacing bits are designed to cut a flat surface, used to do a first cut on the stock to level and smooth it out and also used to give your Spoilboard a perfectly flat and level surface. Larger diameters tend to give a flatter finish, but also take more power!
Ball Nose | Instead of a flat or nearly so cutting end these are rounded which gives better results on relief carvings. If you use them to clear out material from a pocket, they will leave small ridges where cuts overlap.
Upcut | These have the groves on the bit arranged so they pull any cutting debris (swarf) upwards, away from the bottom of the bit. Good for machining hard materials but can lift the top of the stock a little causing a ragged edge, especially for example in Plywood.
Downcut | These have the groves on the bit arranged so they push any cutting debris (swarf) downwards, towards the bottom of the bit. Bad for machining hard materials but can make the cut on the top of the stock cleaner, especially for example in Plywood.

Selecting the right bit for an operation is very important! If you want to engrave some lettering, well think first of using an engraving bit, a 3mm router bit will only cut as a minimum 3mm grooves. Also you can’t cut a square groove with a V or round nose bit; it just can’t get down to the corners.

Search for help. I found useful http://www.tinkerandfutz.com/a-guide-to-cnc-bits/ But remember their router is bigger and more powerful than yours so don’t try the 2 ½ inch surfacing bit on a 3018 Pro!

Also https://youtu.be/xtqgSZlM65k is a well worth watching guide to the bits that SainSmart currently sell (at the time of writing).

## Software

The big question, so far all we have covered is the router and Candle to set it up.

There is loads of it out there, what you find best is going to be very personal, depending on what you want to do and how you like the software to work. All the software has its own quirks, expected user level and capabilities. The simpler the software normally the easier it is to learn, but it can often be restricted in its capabilities, are you designing a jewellery box or a space shuttle? Depending on the answer your software choice will probably be different.

This is really a separate topic and at some time I may do a survey but that’s going to take a long time.

As a starting point Google “CNC Router Software” there is lots out there.

Some that seem to be frequently used:

- Fusion 360
- Easel
- Carbide Create
- Inkscape
- Lots and lots More.........

Search Google for them, watch some tutorials and take your pick!

## Maintenance

Not a lot is needed but a little never hurts.

- Keep it clean(ish) especially the threaded rods and the guide rods, machining, even using a laser is a dirty business.
- The threaded rods and guide rods will need lubricating every so often to keep things running smoothly and prevent any squeaking or binding. A dry lubricant is preferred to prevent the dust from sticking to the rods.
- Every so often check all the frame, bed mounting and motor mounting bolts for tightness. Also check the tightness of the grub screws in the couplers between the stepper motors and the threaded rods.
- Visually check the bearings on all the guide rods to make sure the bearing guides are not working loose. These are a push fit and if any start to work loose at least apply a dab of glue before pushing them back in, preferably wait until a groove appears and then carefully lever the bearing completely out, clean it, apply epoxy thinly round the grooves and then push it back in.

## What to do next

Well enjoy experimenting with and using your router!!

I would suggest making a Spoilboard (See Introduction to CNC for a Total Novice – Making a Spoilboard) and if you are using a laser Introduction to CNC for a Total Novice – Setting up a laser. Other guides are available!

## Acknowledgements

I would like to thank:

- All those involved (too many to list) in creating Grbl, releasing it as a free to use Open source project and supporting and improving it.
- Denvi for creating, improving and supporting Candle as a free to use Open source project.
- Arkypita for creating, improving and supporting LaserGRBL as a free to use Open source project.
- SainSmart Customer support for all their help and standing behind their product.
- All members of the SainSmart Genmitsu CNC Users Group on Facebook, both for answering my stupid questions, showing inspiring examples and asking questions that made me think.
- Steve Harhai for taking the time to review this and make suggestions to improve it.

This is not intended as a definitive manual but it may help with some of the principles and techniques involved. If nothing else writing this down has clarified my understanding.

Any comments, proofreading, other ideas or discussions welcomed.

Regards

Graham Bland.

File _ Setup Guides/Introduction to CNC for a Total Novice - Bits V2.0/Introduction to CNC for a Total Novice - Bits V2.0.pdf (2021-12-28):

Introduction to CNC for a Total Novice - Bits | V2.0 | January 2021 | 1

# Introduction to CNC for a Total Novice

Part of a series by Graham Bland

## Bits

## Contents

Introduction to CNC for a Total Novice - Bits | V2.0 | January 2021 | 2

Introduction to CNC for a Total Novice - Bits | V2.0 | January 2021 | 3

Introduction to CNC for a Total Novice - Bits | V2.0 | January 2021 | 4

## Changes from V1.0

Greatly expanded the ER11 collet description and include details on how to fit and change a collet.

## Introduction

I have been playing around for a while but decided it was time for me to learn about Bits and finally understand what the terms actually mean and how they relate to each other.

### This won’t tell you what speed and feed settings to use to cut, but will describe and explain all the information your CAM software asks for and

hopefully explains what it all means.

This guide is meant for users of small CNC routers typically 3018’s but may be of use to others.

The maximum no load spindle speed for my 3018 PRO is ~8,250 RPM, for the 3018 PROVer it is ~9,250 RPM, using the updated GS 775M motor will give ~20,000 RPM. All are low power motors running at 24V. In any examples I am assuming a maximum spindle speed of 10,000, just for the sake of round numbers. Your router may have different speeds depending on the quality and specific type of the spindle motors.

Just for reference the power of the stock spindle motor is less than 100Watts or 1/8HP. The machines for which the ‘normal’ CNC bit guides are written will range from, well let’s just say 1HP or 800W is a low powered machine.

Also there are other considerations, I am limiting this guide to what I would call affordable bits. My router was not expensive so I am not really interested in using ‘professional’ bits at more than £50 each, even if I could fit them into my ER11 collet holder. (Actually I am not really interested at £25 each, that was just a random figure, and I definitely do not have a poster of a 6 flute 25mm long end mill using internal coolant on my bedroom wall)

I am using free to use software here wherever possible (Apart from Windows of course). NOTE: I mean free to use for me as a non commercial hobbyist, for example I am using Autodesk Fusion360 and have a free licence as long as I don’t try and make any money out of it, that’s fine as a full licence would be hundreds of pounds a year and it’s a hobby. Any software which has a free version and a subscription version, well I am referring to the free one unless specified.

I am producing this as a document, mainly because It is an edited series of notes I made, partly because I am tired of watching instructional videos on YouTube which play at Mach 2 and so I am constantly stopping, rewinding and re-watching. Also I have been told I have a body made for Radio, a voice most suited to the Deaf and I still haven’t worked out how to use the video camera on my phone properly.

### My Background

- I am a retired IT guy, started as a trainee programmer using an IBM 360/40 a long, long time ago (the /40 designation meant it had ~ 40k memory, massive at that time).
- Until recently if I wanted to design something I would use pencils, paper, compass and ruler.

Introduction to CNC for a Total Novice - Bits | V2.0 | January 2021 | 5
- I did get 98% on my last woodwork exam and the table I made is still in use, but that was an even longer, long time ago.
- Always been keen on making things and trying to understand how things work.

### Disclaimer

Yeah nowadays it has to be included, and it makes sense as I accept NO liability for anything I may say, write or think.

1. I am a total novice (or was when I started out). I MAKE NO CLAIM THAT ANYTHING I SAY IS CORRECT! All this is based on searching the Internet, forum comments.... and my own experiences.
2. I am not a professional machinist, just a hobbyist trying to make sense of the world around me and make nice things. If you disagree with anything in here for any reason, please let me know.
3. While I do not work for, or am associated with SainSmart in any way they did provide some samples of bits for me to review and update this series of guides.
4. These are power tools, sharp pieces of metal designed to cut things while rotating at high speed and throwing small bits away also at high speed. Keep everybody’s fingers out! A wood chip flying up your nose is nothing to be sneezed at, never mind in one of your eyes.
5. Take account of the materials you are using and take adequate precautions, dust and ashes can be harmful.
6. I work in mm. Why anyone still uses inches for design work is a mystery. But then I still think of temperatures in Fahrenheit, anything beyond 500m in miles and property plot sizes in acres!
7. I have been told by lots of people that my sense of humour is at the least a bit strange. I do not apologise for it.
8. Any corrections, clarifications or discussion welcome. You can find me on the Facebook SainSmart Genmitsu CNC Routers Group as Graham Bland. https://www.facebook.com/groups/SainSmart.GenmitsuCNC/

### Accompanying files

NOTE: Facebook has a problem, it will not allow compressed files (.zip, .gz, ......) to be uploaded to the Files section of any group, but it bases this decision solely on the file extension, not the contents.

It is easy to bypass this by changing the file extension before uploading, I use .zip files, and rename them to .zipp This means that after downloading you will have to reverse this by renaming any xx.zipp file to xx.zip, windows will issue warnings that you are probably going to make the file unusable, just ignore it and rename anyway. Then you can open and extract the files as you wish.

So you there may be 2 versions in the files section. One an xx.pdf which is the basic words, and if there are any accompanying files with it an xx.zipp with the .pdf and everything else.

Accompanying files for this guide are:

Tool library for Fusion 360 with all SainSmart bits. | SainSmart Master V1.tools
Tool library for Vectric V-Carve Desktop with all SainSmart bits. | SainSmart Master V1.vtdb
The raw bit data for the tool libraries | SainSmart Master Bit Data V1.0.xlsx
Basic tool feed and speed calculators and V-Bit and Ball nose bit Width vs Depth calculations. | Simple Bit Calculators V1.0.xlsx

Introduction to CNC for a Total Novice - Bits | V2.0 | January 2021 | 6

### Other files in this series

All these are in the files section of this group (https://www.facebook.com/groups/SainSmart.GenmitsuCNC/),
there may be more or less as I am not going to update everything if I add a new one or remove one.

They can be found in the files section of the Facebook group by searching for ‘Introduction to CNC for a Total Novice -’ Or ‘Introduction to CNC for the Total Novice -’ Consistency has never been one of my strong points, just search for’ Introduction’!!

Title | Contents | FaceBook link
- Getting Started | Introduction to the process and how to check and test your 3018. READ THIS FIRST! | https://www.facebook.com/groups/SainSmart.GenmitsuCNC/permalink/2352850398359114/ (https://www.facebook.com/groups/SainSmart.GenmitsuCNC/permalink/2352850398359114/)
- Making a Spoilboard | Example of how to cut, fix, face and engrave a 3018 Spoilboard with specific instructions for 3018-Pro and PROVer. | https://www.facebook.com/groups/SainSmart.GenmitsuCNC/permalink/2451607738483379/ (https://www.facebook.com/groups/SainSmart.GenmitsuCNC/permalink/2451607738483379/)
- Setting up a Laser | Fitting, focussing and starting out with a Blue Diode Laser on your 3018. | https://www.facebook.com/groups/SainSmart.GenmitsuCNC/permalink/2356427874668033/ (https://www.facebook.com/groups/SainSmart.GenmitsuCNC/permalink/2356427874668033/)
- Tuning Grbl Settings | Exploring the optimized settings for your 3018 to make it faster and better. | https://www.facebook.com/groups/SainSmart.GenmitsuCNC/permalink/2373672706276883/ (https://www.facebook.com/groups/SainSmart.GenmitsuCNC/permalink/2373672706276883/)
- Spindle Speed and Laser Power | The relationship between the Spindle Speed and Laser power of your 3018 and how to set the values. | https://www.facebook.com/groups/SainSmart.GenmitsuCNC/permalink/2531618443815641/ (https://www.facebook.com/groups/SainSmart.GenmitsuCNC/permalink/2531618443815641/)
- Basic GCode for Grbl | Introduction to GCode on Grbl based routers plus non GCode control commands. | https://www.facebook.com/groups/SainSmart.GenmitsuCNC/permalink/2705472216430262 (https://www.facebook.com/groups/SainSmart.GenmitsuCNC/permalink/2705472216430262)

Versions of a lot of these along with more information and resources, yes there are other people who do this sort of thing, can be found at https://docs.sainsmart.com

### Units

I work in mm, rates of movements on routers are usually expressed as x per minute so that’s what I use here (anyone coming from a 3D printing world, well they normally use x per second). Other units do exist, are readily available and can be easily converted.

## The Basics

How does a router bit work? Well it has sharp cutty bits mounted on a shaft which when rotated and pushed into the stock cuts bits out of it which are carried away by the spaces on the cutter! Pretty obvious but please read on, this does get a little more interesting!

Bits come in a bewildering variety of shapes and sizes and an even greater variety of names and descriptions, often there is more than one name for basically the same thing. So let’s start with the more common shapes or types of bits used on hobby machines. Your CAM software will have names and definitions for the types of bits it knows how to use. These vary between CAM software suppliers.

### Common shapes of bits

These are the most common and here I am only describing the shape of the cutting surfaces and so the shape they will carve out of the stock. Each of these can have lots of variances but the basics remain the same.

V (AKA V Groove, Chamfer Mill, Engraving)

Introduction to CNC for a Total Novice - Bits | V2.0 | January 2021 | 7

It will cut a V shaped groove into the stock the angle of the V is normally referred to as the angle between each side of the groove. Also you may see a tip radius or diameter specified, this would be a small flat spot at the tip of the bit, often these are called Engraving bits.

End Mill (AKA Flat End Mill, Straight Mill, Slot Drill)
Basically a straight rod, it will leave a flat bottomed square groove as it cuts. Lots of variations in shape such as fishtail which describes the shape of the bottom face.

Ball End (AKA Radiused Slot Drill, Ball Nose, Lollipop)
A round ended bit where the circular cutting edges extend past the vertical. Some software doesn’t allow this so the closest specification would be a Ball Nose which is mostly close enough.

Ball Nose (AKA Round Nose) An end mill with a hemispherical end. OK an end mill with half a ball stuck on the end.

Bull Nose (AKA Radiused End Mill) An end mill with a cutting edge radiused at the edges.

Tapered Mill (AKA Dovetail Mill)
Where the edges of the bit are tapered, not vertical. This will have a shape on the tip such as a tapered ball nose, flat nose, bull nose.... The advantage of a tapered bit is that they tend to be more robust, but they are not going to cut a vertically edged pocket. A dovetail Mill normally has a negative taper angle, the wider portion being at the tip.

Surfacing Mill (AKA Face Mill) Really these are just big end mills, the cutting edges are designed to leave a
flat surface and the larger diameter reduces the ridges which can be left by a smaller diameter bit.

Others
Lots of these exist for many reasons, but especially when starting out you are unlikely to need a Radiused Square End 23 degree Shallow Ogee bit.

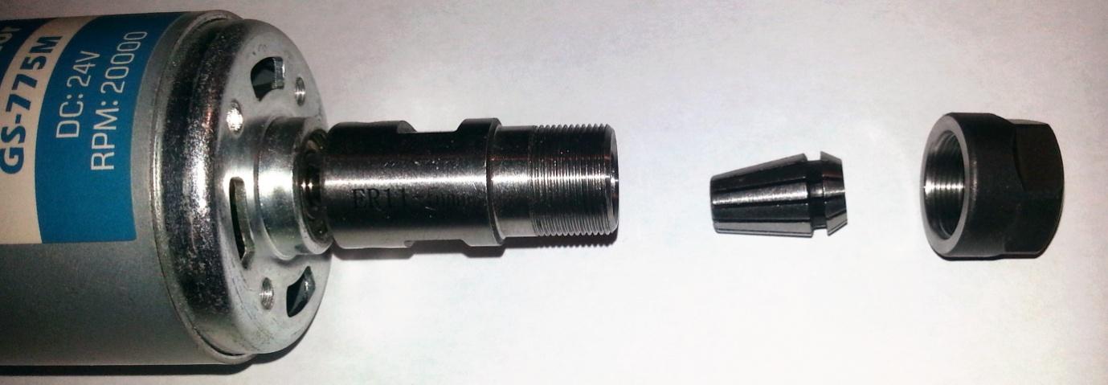
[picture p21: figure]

Introduction to CNC for a Total Novice - Bits | V2.0 | January 2021 | 8

There is one however which is worth mentioning here is a Form Mill. Only normally supported by higher end CAM software this lets you define a line or form which describes the shape of the bit.

You might have noticed the beginnings of potential confusion already. Well hopefully not confusion but a blurring of the boundaries. For example what is the difference between a V Bit and a tapered mill with a very small tip diameter, or an end mill and a surfacing mill........

The simple answer is not a lot; just pick the closest match in your CAM software. For example if it has a V bit definition well a 0.1mm tip diameter is not going to make a lot of difference for 99.99% of the things you are doing but you may find an Engraving bit allows you to specify the tip diameter.

Like many things the descriptions and terms used to describe CNC bits and their properties are diverse and many words which basically mean the same are used. This is not a thesaurus but I have tried to mention all the common terms I have come across.

## ER 11 Tool holder and collet

Not strictly part of the bit but very important. What the ER 11 collet system is on your router and how to use it. This is very important to ensure your bit is mounted correctly. This is the ‘standard’ tool holder for small routers. ER is the ‘name’ 11 means that it has an 11 mm diameter at the bottom of the taper in the holder.

Why is a collet system is used, why not just mount a chuck which would be more versatile and easier to adjust? A Collet system will:

- Clamp the bit more firmly.
- Give a superior alignment of the bit within the holder.

The drawback is that the size of the collet used must be matched to the diameter of the bit shank, but different sized collets are relatively cheap.

It has 3 parts, Holder, Collet and Clamping nut:

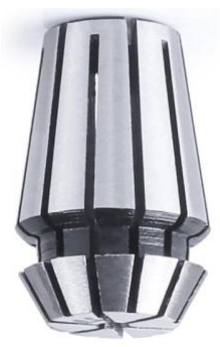
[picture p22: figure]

Introduction to CNC for a Total Novice - Bits | V2.0 | January 2021 | 9

### Holder

Normally factory fitted onto the motor shaft as it is a very tight or interference fit onto the shaft in order to keep it exactly aligned. It is further held by two grub screws tightened onto the motor shaft. It can be removed and replaced but will probably require heating to slacken the fit and the very careful application of force to avoid damaging the motor.

It has a tapered interior which matches the angle of the collet so that as the
collet is forced into the holder the collet is compressed and clamps round the shank of the bit. A threaded area at the bottom to match the clamping nut and a couple of flats allowing a spanner to be used to tighten and release the collet.

### Collet

The Collet fits round the shank of the bit and slides into the tapered interior of the holder. Near the bottom is a groove which fits into the clamping nut and at the bottom another taper which matches the clamping nut. The slots cut through the collet allow the segments to be forced inwards round the bit as it is tightened into the holder. There is obviously a limit to how much it can be compressed meaning the hole through the collet must match the diameter of the shank of the bit.

### Nut

Not just a simple flanged nut, the design of the interior is important.

At the base there is a bottom taper, this matches the taper angle of the bottom of the collet and ensures as it is tightened the collet is compressed evenly.

Above this is a retaining ring, this is very deliberately made wider at one side
than the other, it’s not supposed to be concentric to the nut. This retaining ring
fits into the groove of the collet. This holds the collet into the nut and also when you wish to remove a bit it forces the collet down out of the taper of the holder breaking any ‘cold welding’ which may have occurred and so releases the clamping round the bit allowing it to be removed easily.

The simple reason that the retaining ring is offset within the nut is to allow a collet to be inserted and removed.

### Collet Sizes

ER11 Collets are described by the internal diameter. So a 3mm collet is designed for a bit with a
3mm shank diameter. There is a bit of tolerance built in due to the clamping action so a 3mm collet will also take a 1/8 ” or 3.175mm shank. A 1/4” shank is 6.35mm so it’s closer to the tolerances but a 6mm or 7mm collet should work. Depending on the bits you use get the collets to fit them, if you frequently use 6mm bits then get a 6mm collet, if you often use 1/4” bits get a 1/4” collet, if you use both, get both.

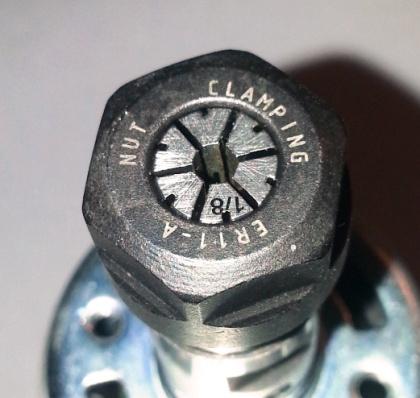
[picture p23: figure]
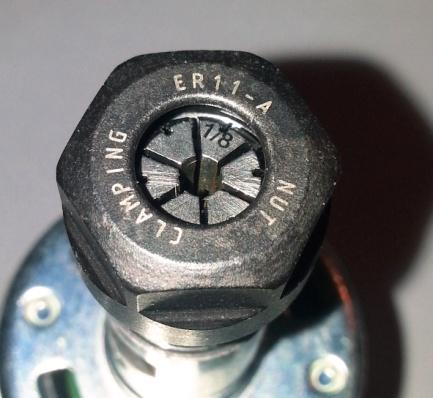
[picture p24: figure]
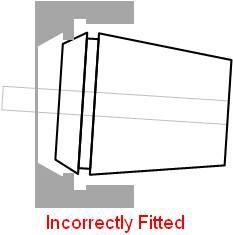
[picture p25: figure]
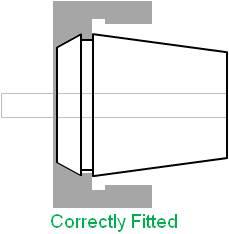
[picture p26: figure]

Introduction to CNC for a Total Novice - Bits | V2.0 | January 2021 | 10

Collets are also available in sets which can be cheaper and very useful if you also use drills. https://www.sainsmart.com/products/genmitsu-15pcs-er11-precision-spring-collet-set

### Changing a collet

Removing a collet
First remove any bit and unscrew the clamping nut completely from the holder. The collet now needs to be popped out of the retaining ring by pressing the collet over to the side (1) and then applying a push to pop it out (2).

It will depend on where the direction of the sideways push is. It will be easiest
to push out when you are lifting the collet slot over the narrowest point of the
retaining ring on the nut as shown by the orange circle. As you cannot see where this is if it doesn’t pop out at the first attempt rotate it a bit and try again.

Inserting a new collet
Before inserting a new collet make sure;
- The inside of the tool holder is clean and free from dust and debris.
- The collet itself is clean, on the outside of the tapers, in the spaces between the collet segments and in the bore which will take the bit.
- The nut is clean and free from debris around the retaining ring and on the bottom taper.
- Do not insert a collet into the nut with a bit inserted into the collet! This will limit the amount the segments of the collet can move and will make it nearly impossible to seat the collet into the nut correctly.

Locate the widest point of the retaining ring in the nut and engage the slot of
the collet into it, while pushing it in to the nut (1) press it straight (2), it will ‘clip’ in. After insertion check that the collet is straight and is fully seated into the nut.

Introduction to CNC for a Total Novice - Bits | V2.0 | January 2021 | 11

The left photo shows a correct alignment with the collet aligned with the nut and the bottom taper sitting on the corresponding part of the nut. On the right the collet is not aligned with the nut, the bottom taper is resting on the retaining ring rather than it being in the slot of the collet. When tightened from this position the collet will be forced out of alignment and damage to the nut, collet and tool holder could result.

For ease of use I have purchased an ER-11A clamping nut for each collet. This means I can just leave the collet permanantly in the nut. https://www.sainsmart.com/products/genmitsu-4pcs-er11-a-collet-clamping-nut (https://www.sainsmart.com/products/genmitsu-4pcs-er11-a-collet-clamping-nut)

### Inserting a bit

- Make sure the nut is slack on the tool holder.
- Make sure the shank of the bit is clean.
- Slide the shank into the collet, the maximum depth of the bit the collet will clamp is 18mm (some collets may have a shorter clamping distance). There is a gap between the top of the collet in the tool holder so a bit can be inserted further if required.
- Using the spanners firmly tighten the nut onto the holder, compressing the collet around the bit. This does need to be tight.

### Checking everything

After mounting a bit, especially after changing the collet, manually rotate it and ensure the rotation of the tip of the bit is straight and true.

If it is not check:

- The collet is seated correctly in the nut.
- A dirty bit shank or collet interior is not throwing things out of true
- The tool holder taper and collet exterior are clean
- The collet is the correct size for the bit shank
- The collet has been tightened enough and holds the bit securely
- The bit is not bent or damaged.

If excessive vibration occurs when the spindle is turning a process of elimination can identify the cause. Remove the nut, collet and bit from the holder and try again. If the vibration persists check that the holder is straight and secure on the motor shaft, if it still persists then the motor itself is the suspect.

Remove the bit from the collet and reattach the nut and collet into the holder and try again. If the vibration persists check the collet mounting into the nut. If it goes away check that the collet is the correct size for the bit shank or try a different bit.

NOTE: These checks should be made without performing any cutting. If excessive vibration occurs when cutting it is often due to over stressing the router with the depth of cut and/or feed rate being too high.

Introduction to CNC for a Total Novice - Bits | V2.0 | January 2021 | 12

## Bit Dimensions and definitions

Why is this important? Well for any CNC machine your CAM software needs to know some things to generate a toolpath, which are instructions on how to move the centre and tip of the bit around to achieve the desired result. Things like the diameter of the bit are very important so it can work out how to cut out the shapes and contours you want. The shape of the bit is also important so it can calculate how deep it needs to be to achieve the desired contours, can it cut a vertical edge....

Things like how deep is your bit capable of cutting before, for example, a thicker shaft starts rubbing against things it should not touch so it can show an error rather than just proceeding, well that depends on the complexity of your CAM software. It’s still important but a lot of the simpler 2.5D CAM software just ignores the problem which means it is down to you to prevent it from happening.

Some of the speeds and feeds you will use depend a lot on the bit you are using and its physical characteristics, you will break a lot more bits if they are long and thin than if they are short and fat! So size is important.

So let’s look at some of the makeup and dimensions of a typical bit.

### Shank or Shaft

The round piece at the top of the bit that goes into the collet, the shaft diameter must match the collet in use (See above).

### Overall Length

Length of the bit from top to tip.

### Stickout (aka length below holder)

How far the bit sticks out from the end of the tool holder. The maximum length that the collet can clamp is 18mm, the length that can go into the tool holder is ~25mm. The Stickout and the positioning of the Spindle motor in the holder needs to be long enough to reach the bottom of the cut with the Z axis at its lowest and still to clear the top of the stock with the Z axis at its highest.

Keeping the Stickout as short as is necessary helps reduce flexing of the bit increasing accuracy, reducing wear and the chances of bit failure.

### Shoulder length

Especially in the case of small diameter bits the shaft diameter will be larger than the cutting diameter, the shoulder length is the lowest of how far from the tip this change starts. Effectively this is the maximum depth a bit can go vertically into the stock material, not as far as it can cut effectively though.

### Flute Length

This is the maximum height of the working range of the flutes from the tip of the bit. This is not the same as the length of the spirals from the tip as these normally continue up a bit more than they can effectively work.

Introduction to CNC for a Total Novice - Bits | V2.0 | January 2021 | 13

### Maximum Depth of Cut (DOC)

Simply how far down the bit can effectively cut, this is normally the smallest of the flute length and shoulder length for a straight edged bit. If you are using a Vbit for example this would normally be the maximum depth at which it will cut a V before just starting to leave a round hole. DOC is also used to describe the distance the bit is actually instructed to cut in a single pass but for a bit definition it’s the maximum depth it can cut.

### Flutes (AKA Teeth)

The number of cutting surfaces on the bit, this is usually 1 to 4 but can be higher, Burrs can get well into the teens. Used in speed and calculations to determine things like how big the chips are going to be and it will affect surface finish, speeds.....

### Diameter

Simple the diameter of the cut or slot the bit will make, well not so simple in practice, what is the diameter of a V Bit? It changes from the tip to the top! So this depends for some bits on what CAM software you are using.

### Corner Radius

Normally applicable to bull nose bits, the radius of the corner between the tip and the side of the bit.

### Taper and other angles

Just angles but depending on the type of bit and CAM software. BUT the angles can be expressed in different ways! Normally a V bit angle is measured by the angle of the groove it will make from edge to edge, often referred to as the Included Angle. But for a tapered bit it is normally measured between one edge and the vertical or the half angle.

### Spirals

The spirals on a bit have a simple job, to remove the chips away from where it is cutting so the bit does not get clogged. Something like a V bit doesn’t have spirals as the chips can just move away sideways or upwards by themselves. Well that’s the theory anyway.

But as they will also come into contact with the side of the stock so while they are not exactly cutting surfaces they still rub and so have an effect on the stock.

### Corncob

Where the spirals are shaped to provide extra cutting edges or surfaces to break up the ships more, or both. Think of a cob of corn but with sharp kernels arranged in spirals rather than straight lines.

### Upcut, Downcut and Compression

This is all about the direction of the spirals on the edges of the bit. The edges of a straight bit will create friction from the rotating spirals and the movement of the chips can cause splintering on the edges of the cut, especially on laminated materials such as plywood or veneers and others.. It can also leave a lip on softer materials.

Introduction to CNC for a Total Novice - Bits | V2.0 | January 2021 | 14

Upcut
The standard bit type, just like a drill the spirals move the chips UP away from the cutting edge. If a bit description doesn’t mention any cut type it’s probably an Upcut. Can cause a bad finish at the top of the stock.

Downcut
The spirals move the chips DOWN towards the cutting edge, this means that the action of the spirals on the edge of the material is downwards which can help prevent splintering or the creation of a lip at the top, but if you are cutting all the way through a material can transfer the splintering/lip to the bottom surface.

There is a major consideration when using these in that the chips still need to be moved away from the cutting edges to prevent clogging. Having them leave at a side is the only option so don’t use them to plunge or drill into the stock!

Compression
Well you have a cut that using an Upcut bit leaves the top ragged but when using a Downcut bit leaves the bottom ragged. Use a compression bit, Upcut at the bottom and Downcut at the top!

That is a compression bit in a nutshell, disadvantages are that all the chips meet somewhere in the middle hence the compression name so make sure there is some way for them to get out.

Normally these will have a short Upcut section at the bottom and a longer Downcut section at the top rather than a meet in the middle design as this allows much more flexibility in machining different thicknesses of stock.

### Material

What the bit is made of not what you are cutting. A basic rule of thumb is that the bit must be a lot tougher than the material you are cutting but there are a lot of other factors such as rigidity, wear resistance and don’t forget cost.

HSS
Called High Speed Steel because it can be made very rapidly This is pretty much a generic description for a modern steel blend designed mainly for high speed tools.

Carbide
Carbide tools are formed from a tungsten (or other metals) and carbon powder. This has a very high wear resistance and so keeps sharp for longer but it is also expensive. Often a tool will be made from HSS with just the cutting surfaces made from Carbide. Because of the cost pure carbide is not normally used by hobbyists.

Tungsten Carbide Steel
A High Speed Steel with carbide blended in to make it more wear resistant.

### Coatings

A coating can be applied to the bit to enhance mainly to enhance its resistance to wear, reduce friction heat transfer and finish quality.

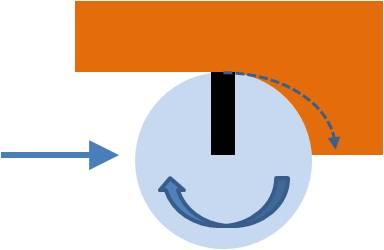
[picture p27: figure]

Introduction to CNC for a Total Novice - Bits | V2.0 | January 2021 | 15

Nano Blue Coat
A high performance Nanograin (very small particles) carbide and silicon coating giving 2-3 times better tool life than a micrograin carbide coating.

Titanium
A titanium nitride coating to enhance cutting performance and wear. This has a gold colour.

Others
There are a myriad of other options including no coating, the differences between them are beyond my comprehension and best left to materials scientists and professional machinists!

## Milling and routing terms

Some questions that need answering to get good (or bad) results are how fast is it turning, how big is it, how fast is it being pushed into the stock and in which direction, how many flutes, what do the spaces or spirals do with the waste material, how deep is it cutting, what is it cutting......?

### Splintering

Mainly for laminated materials this refers to the action of the bit as it cuts causing the top (or bottom) surfaces to separate slightly and results in splinters on the surface. Other materials can do this as well, normally hardwoods, softwoods can have ‘strings’ left on the edges of a cut, which is basically the same.

### Climb vs conventional milling

Lets start with a router bit, flat end, straight edges on the shaft, one flute at the bottom, spirals round the edges to remove the chips and 3mm in diameter, or in other words a 3mm single flute flat end mill.

It will be turning clockwise, that is traditional and small router controllers will only turn the motor in a single direction which is clockwise. In very simple terms the bit is being moved into the stock at a constant speed while rotating clockwise.

Climb vs Conventional is a term used to describe which direction the bit is being fed into the stock.

Conventional milling

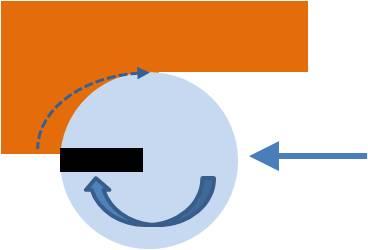
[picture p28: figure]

Introduction to CNC for a Total Novice - Bits | V2.0 | January 2021 | 16

Each flute will carve out a chip from the stock as shown by the dotted line due to the movement and rotation of the flute as it turns and moves. The chip will start off small and get thicker as the bit moves and rotates.

Climb milling

As for conventional milling but the chip will start out thicker and end up small.

As far as I can tell climb milling gets the name from when using a handheld router it will try and climb out of the stock unless firmly held, but please don’t quote me on that, especially as it is sometimes referred to as down cut, but I suppose if it is cutting down then...!!!

Climb milling will normally leave a cleaner finish with less splintering at the top than conventional milling.

In both cases the thickness of the chip depends on the rotation speed of the bit and the feed rate of movement as well as the diameter of the bit and how far it is cutting into the stock. The chip must then be removed by the spirals on the bit ready for the next cut.

As to what happens during the rest of the rotation while the bit is still moving but not cutting – well it’s turning quite fast so will get round to the next cut before it becomes a serious problem, if it is turning too slowly then it will bend and possibly break.

### Spindle speed

A simple one, the rotational speed of the bit in Revolutions Per Minute, often just referred to as speed.

### Feed Rate

The speed at which the spindle is being moved into or across the stock, often just referred to as feed. The faster you move the bit through the material the quicker it will cut but it will also put more stress on the bit and the machine. If you exceed the federate that your router is capable of for a cut then the stepper motor will skip or lose steps and your work will be ruined.

### Depth of Cut (DOC)

Mentioned as a bit parameter but when cutting it is how deep each cutting pass will be into the stock. The larger the Depth of Cut then more material will be removed on each pass meaning fewer passes are needed, but again larger values will put more stress on the bit and machine.

Introduction to CNC for a Total Novice - Bits | V2.0 | January 2021 | 17

### Max Feed

The maximum achievable feed rate for the router. This is normally set as the feed rate the router is capable of moving the bit, not the rate at which it will cut! For a Grbl based machine this is held in the settings as $110-112 for the X, Y and Z axis respectively, often no more than 1,000mm/min. If you use a value which exceeds the setting then Grbl will just use the setting value instead. Just because it can move at a certain rate does not mean it can cut at that rate!

### Feed per Tooth

Calculated value dependant on the number of flutes and Feed. It’s just Feed / number of flutes. (Please don’t ask why it’s called feed per tooth when the teeth are normally called flutes, just don’t go there, OK?)

### Feed per Revolution

Calculated value dependant on the Speed(RPM) and Feed. It’s how far the bit moves along the cutting path in a single revolution. It’s Feed/RPM and is expressed in mm.

### HorsePower or Kw

The power of the spindle motor, measured in HorsePower or Kw. The ‘standard’ power of the ‘standard’ 775 spindle motor on a 3018 is around 60W, or 0.06Kw, or 0.08HP. Think more of Hamster Power!

### Stepover

The distance the bit is moved sideways between each cut or line. This can be expressed as either an absolute distance or a percentage of the bit diameter depending on your CAM software. 0 would mean that the bit would just retrace the previous cut, anything
over the bit diameter or 100% would mean that ridges would be left between each cut.

A good rule of thumb is 40-50% of the bit diameter, lower values increase the machining time but give a better finish quality.

### Stepdown

See Depth of Cut! The distance the bit is moved down after each layer has been cut. This depends on the material and bit, the greater the Stepdown the faster a pocket will be cut as it will take fewer passes but will increase the stresses on the bit and the machine. These are small machines so use small values to start, 1mm is quite massive on these small machines but it depends on what you are doing to what.

### Ramp

Where the printer gradually applies the Stepdown as a ramp rather than plunging and then cutting horizontally.

### Lead in and out

The way the bit is moved into and out of the cut, the options you have depend on your CAM software. Often a separate spindle speed and feed can be specified for lead in and lead out operations.

Introduction to CNC for a Total Novice - Bits | V2.0 | January 2021 | 18

### Plunge

Moving straight down or plunging into the stock. Normally used as a lead in/out method, though it could apply to drilling. This is the most aggressive lead in method. NOTE: Do not use with compression or downcut bits! They move the chips down and so when plunging leaves them with no way to leave the cut and will cause the bit to clog, overheat...!

### Spiral and helical

Other lead in methods, once will lower the bit in a spiral ramp, the other will use a helical ramp. These terms can also be used to describe the toolpath used, normally for roughing operations.

### Chatter and Sawdust

In an ideal world the bit moves through the stock with each flute carving out a distinct chip removing the stock cleanly and the chips carry away the heat generated by the bit action without overstressing the machine or wearing out bit too much.

Sawdust
What you get when the chips are too fine, basically they stop being recognisable chips and become sawdust. You can reduce this by slowing the RPM and/or increasing the feed rate so that the bit is cutting larger chips.

Cutting too small chips can greatly increase the heat generated by friction between the bit and the stock as the chips are supposed to carry a lot of the heat away.

This can be especially important when cutting materials such as plastics with a low melting point where it’s not so much sawdust as the bit looking like the centre of a candyfloss machine due to the material melting.

This can be reduced by decreasing the RPM, increasing the feed rate, possibly increase the depth of cut. It is advised to only change one at a time and see what happens.

Chatter
What you get when the chips are too large. Called this as the machine is overstressed trying to push the bit it starts to make chattering noises.

This can be reduced by increasing the RPM, decreasing the feed rate, possibly decrease the depth of cut. It is advised to only change one at a time and see what happens.

### Roughing and finishing

Imagine you are trying to make letters in relief, so you have a lot of material to remove around them, but also want fine detail around and in the lettering.

If you try and make a large carving just using a 0.5 mm bit it may come out well, but there is a chance you will expire from old age before it is complete.

So the first pass is with a bigger and coarser bit (roughing), this removes the material much quicker but doesn't give as good a finish. So you tell your CAM software to leave a small margin around all the surfaces.

Introduction to CNC for a Total Novice - Bits | V2.0 | January 2021 | 19

This is followed by a second pass with a smaller or different shaped bit (finishing), it will fit into all the nooks and crannies, go round the edges, smooth the surfaces.... but although it will be slower it doesn't have to remove large swathes of material!

The major drawback is that you have to change the bit between the passes. If you carefully change the tool without manually moving anything on the XY then the XY axes 0 position should not to be changed. If you have limit switches it’s a good idea to write down the machine coordinates after positioning the XY axes on the first pass so that you can always home, then jog back to the same coordinates and reset the XY work origin.

The new tool will need a reset of the Z axis zero so it's wise to set the original Z zero somewhere where it can be reset after the roughing pass has completed. Remember the Z zero does not have to be set in the same XY coordinates of the work origin.

How to generate roughing and smoothing passes is totally dependent on the CAM software you are using. Some will support a number of passes not just 2!

### Surface speed (AKA Cutting speed)

This is just the speed that a single flute at the circumference of the bit travels across the surface of the stock. It is calculated by RPM * bit circumference so a 3mm dia bit has a circumference of π*Bit Diameter or in this case 9.42mm so at 100 RPM the surface speed is 942 mm/min, the bigger the bit the faster the surface speed will be (at the same RPM of course).

Surface speed also generates heat by friction which can be especially annoying when cutting materials with a low melting point like plastics.

### Chip Load

This is a measure of the thickness of the chip that each flute will carve out of the stock. It is calculated by Chip Load = Feed Rate / (Spindle Speed * Number of flutes). As you can see Chip Load does not depend on the diameter of the bit BUT larger bits can normally take a larger Chip Load simply due to the fact that the flutes will be larger and the bit more rigid. If the Chip Load is bigger than the size of the flutes you will have problems.

If you have a recommended Chip Load for a bit then you can determine a range of speeds and feeds to supposedly give the same results.

NOTE: The size of the chips or Chip Load is especially important for materials such as plastics which have a low melting point. This is because cutting generates heat by friction between the bit and the stock. The chips help to carry away this heat from the stock and so prevent it from melting so a larger Chip Load is beneficial for these materials.

### Runout

Runout is the difference between the diameter of the bit and the distance it will cut when rotated. A professional machinist will probably measure this using an, often expensive (cheap ones are available), dial guage by comparing the distance measured to the bit as it rotates. Well I don’t have a dial guage and can practically ignore this on my 3018’s as they are not designed for precision machining, well unless I can see a wobble at the end of the bit.

Introduction to CNC for a Total Novice - Bits | V2.0 | January 2021 | 20

## Setting up your CNC software

This is important as your CAM software needs to know what bit you are using before it can generate a toolpath, Mainly it needs to know the shape as well as what speed and feed to use. At the simplest level it will, quite rightly, not even try and fit a 3mm diameter bit into a 2.5mm gap. It may also use the bit dimensions for things like checking the maximum cutting depth, is the shank of the bit going to hit anything.......

All CAM software has a slightly different way of defining the bit, some are more expansive, some more limited in what bits they can understand.

Generating the movements in a toolpath is all about the shape and size of the bit in relation to the pattern you are cutting, this makes no difference if the bit is made from steel, carbide, or even cardboard, it’s just moving it around so that the stock is cut in the right places to produce the correct result. Imagine you wish to cut a round pocket 10mm in diameter. To work out the correct tool path the CAM software has to know the diameter of the bit to leave the correct sized hole. If you set up a tool path saying you are using a 3mm bit and fit instead a 6mm bit the pocket is not going to be 10mm in diameter!

Then there is the adding of speed and feeds, depths, passes etc. All these depend on not just the bit but the material, machine capabilities.... the software may contain some hints, default settings for a particular material but remember that not only does the USDA Wood Handbook lists 49 separate hardwoods, and that’s just hardwoods native to the USA, add softwoods and species not native to the USA and the number goes up and up! Never mind about kiln dried, naturally dried and if the tree grew on a north facing or south facing slope.

There are nearly as many ‘species’ of aluminium and I am not even going to think about plastics.

### Defining the bit in your CAM Software

Nearly all CAM software has a tool library where details of the bits you have can be stored to make life easier. Most CAM software will allow you export from and import to the tool library in bulk which is a simple way of saving your bits and adding new ones.

I would like to say that all the measurements are accurate, they rely both on the manufacturers specifications and my own measurements of the bits I have, but they are small little..... and counting the flutes on the burrs is very tricky especially with my eyesight while trying to hold 2 magnifying glasses and the bit at the same time, even without the varifocals! But I hope any errors I may have introduced will make little difference to the results.

If you find any errors or disagree with anything I have said or have better ideas then please let me know via the Facebook Sainsmart CNC users group.

Introduction to CNC for a Total Novice - Bits | V2.0 | January 2021 | 21

### Common CAM software

Lots of other options are available than those given here but some of the more common ones are with some details of the tools they can handle.

Feature | Carveco Maker | Fusion 360 | Vectric V-Carve | Easel
Export Tools | Y | Y | Y | N
Import Tools | Y | Y | Y | N
Form Tool Support | Y | Y | Y | N
Milling Tool Types | 13 | 13 | 11 | 3
Use user defined tools | Y | Y | Y | Pro mode only
Define tool Holder | N | Y | N | N
Save material default Speeds/feeds | | Y | Y
SainSmart Tool library accompanying | | Y | Y | N/A
- This relates solely to their handling of different bits.
- Which CAM software you use is a personal choice and support for bits may be a minor factor.
- Some of the above relate to use on small hobby machines like the 3018’s.
- SainSmart Tool library refers to a file accompanying this document, not included in the software.

### Telling your software about the bits

This should be straightforward, but, and there is always a but!

Let’s take 2 bits

- 20 degree V bit
- 3mm ball nose bit.

All straightforward, but:

- The types and shapes of bits supported in the each product varies. For Example Fusion 360 doesn’t have a V bit type, it does have for milling Tapered mills and chamfer mills and Countersink bits for hole making....
- For a ball nose bit what is the difference between a 5mm bull nose with a 2.5mm corner radius and a 5mm ball nose bit??
- V-Carve allows the definition of V bits and engraving bits. Should the V bit be defined as a V bit or an engraving bit? It can be used for both purposes so which is correct?

There is a very simple answer – I don’t know! So I have tried to pick what makes most sense to me, I am often wrong!!

### Tool Libraries

At the moment tool libraries are defined for Fusion 360 and Vectric V-Carve. I also include the source spreadsheet of tool dimensions to make it easier for you to define the bits in your own CAM software.

Tools which would have to be defined as Form tools are not included, Bit types which cannot be defined are ignored.

The Tool Library is named ‘SainSmart Master’ and can be imported. I then suggest you create another group in your tool library called something like My Bits and copy the tools you possess into

Introduction to CNC for a Total Novice - Bits | V2.0 | January 2021 | 22

that to create a list of the tools you have, organise them how you like so you can select the one you want easily, depending on the software you are using of course.

Fusion 360 Notes
- For a milling operation you must use a milling bit type, a V bit would have to be specified as a chamfer bit or taper mill which are of a milling type, not a countersink bit which is a type for drilling operations.
- An ER11 tool holder is defined in the tool library and used for ALL tools. The shape and dimensions of the tool holder are used by Fusion 360 for collision detection.
- In the Post Processor the tool number and turret are unused – no tool changer on a small router. Manual Tool change and Live tool are always selected.
- Break control and coolant are not supported and so are turned off.
- The default Cutting Data is set, I hope, on the conservative side. Modify this as needed, these are not recommendations!
- Presets for different materials can be added to your tool library later if you want to save your working values.
- The tool name is generated by Fusion 360. It adds the tool cutting diameter and Tool length below the holder to the front of the individual tool description. You can select tools you see by using filters.

Easel Notes
- There is no facility to export or import tools so no tool library can be provided.

Vectric V-Carve Desktop Notes
- The tool name allocated depends on the type and includes minimal information tool type and basic dimensions so there will appear to be duplicates, for example a End Mill (3.175mm) will appear twice being the 1 flute and 2 flute variants. Full details can be seen by clicking on the tool and examining the detailed settings. I have tried to add meaningful names and notes for all the tools.
- The library is organised by the SainSmart bit set Product ID on the assumption that you will copy the tools you have to a different group and organise them as you see fit.
- A V bit does not allow a tip diameter to be specified, an Engraving bit however does but note that the angle defining a V bit is specified as being between the outer edges of the V but for an engraving bit it is specified as the angle between one edge and the vertical, so a 20˚ V bit becomes a 10˚ Engraving bit.
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

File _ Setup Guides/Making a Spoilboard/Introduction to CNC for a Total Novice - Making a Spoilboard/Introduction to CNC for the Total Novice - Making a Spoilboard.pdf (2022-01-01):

Introduction to CNC for a Total Novice – Making a Spoilboard V3.0 March 2020

# Introduction to CNC for a Total Novice

Part of a series by Graham Bland

## Making a Spoilboard

### Contents

### Changes from V2.0

- Changes made to add the SainSmart Genmitsu 3018-PROVer.
- Yes I know the first version was for a ‘Universal Spoilboard’, that was true but only for the Spoilboards then in my universe. A few changes to the model were needed to cope with routers which have an asymmetric cutting area relative to the bed. I am no longer calling the earlier versions Universal! But I am not renaming them.
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

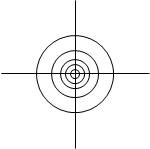
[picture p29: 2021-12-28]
_ Setup Guides/Introduction to CNC for a Total Novice - Getting Started/SingleBitPositioner.jpg

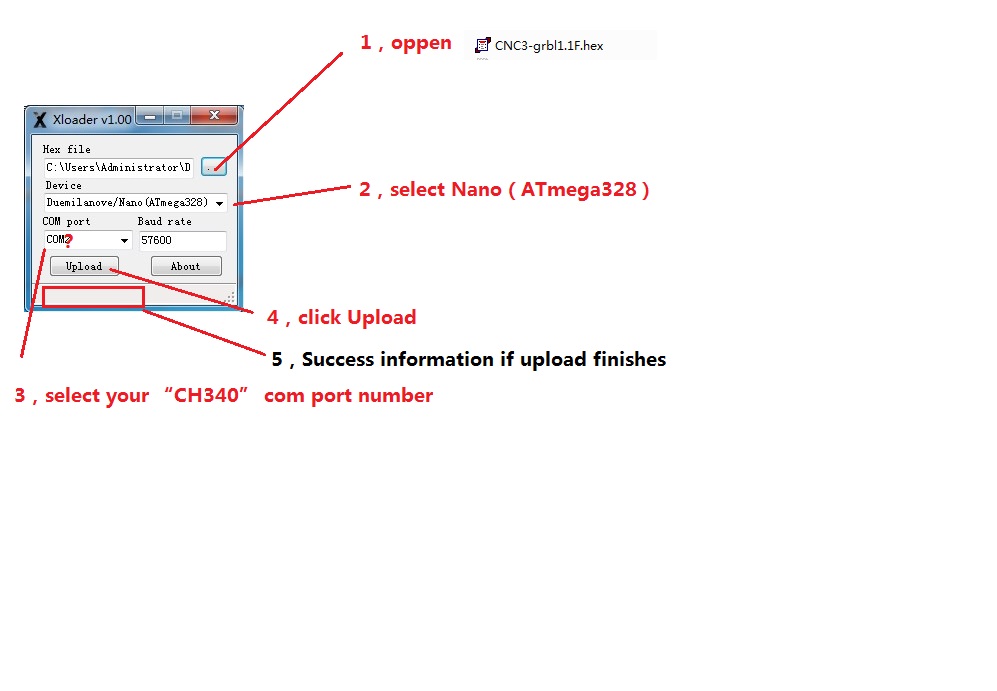
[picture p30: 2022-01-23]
_ Software/Firmware Updated Jan 2022/101-60-280PRO_3018PRO/Firmware upgrade_1.1/XLoader&GRBL1.1F-CNC3/manual.jpg

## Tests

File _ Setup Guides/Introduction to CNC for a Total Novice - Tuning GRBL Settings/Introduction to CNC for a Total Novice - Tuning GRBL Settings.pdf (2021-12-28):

Introduction to CNC for a Total Novice - Tuning GRBL settings V1.0 December 2019

# Introduction to CNC for a Total Novice

Part of a series by Graham Bland

## Tuning Grbl Settings

### Contents

## What this covers (supposedly)

At the end of the GRBL configuration page it says the following:

Finally, tune your settings to get close to your desired or max performance. Start by ensuring your $100,$101, and $102 axes step/mm settings are correct for your setup. This is dependent on your stepper increments, micro steps on your driver, and mechanical parameters. There are multiple resources online to show you how to compute this for your particular machine, if your machine manufacturer has not supplied this for you. Tweak your $12x acceleration and $11x max rate settings to improve performance. Set to no greater than 80% of absolute max to account for inertia, cutting forces, and motor torque reductions with speed. Set your $13x max travel settings if you plan on using homing or soft limits. It's recommended to enter something approximately close to actual travel now to avoid problems in the future.

$100-2 have already been covered in ‘Introduction to CNC for a Total Novice - Getting Started’ along with some other settings. That leaves the acceleration and max rate settings. I am also including Spindle speeds here as well as some others.

NOTE: the acceleration settings section is duplicated in ‘Introduction to CNC for a Total Novice – Setting up a Laser’ as it makes such a difference when using a Laser.

## Introduction

### Why bother, just use the defaults, they work!

Yes they do, mostly, but I first noticed when using a Laser to engrave that the ends of any line were burnt more than the middle, after a lot of investigation I decided that most if not all of this effect was caused by Grbl slowing down the feed rate at the start and end of the lines.

Or in other words accelerating the laser as it travelled across the line as controlled by the $12x acceleration parameters. On playing around with these I also discovered that apart from much cleaner lines the time taken to run a job was greatly reduced, by around 30%, but this is very dependent on the actual job.

The router motherboard was probably not made for your specific router, it was designed for and is normally set up for a generic router. Your supplier may configure some of the settings for the specific router, but it seems that a lot do not. If you are buying just the board as a replacement or an upgrade then the supplier is not normally going to provide it pre configured for your router.

Getting them right makes things work much faster without any unwanted side effects. (As far as I can see)

### Settings covered

- $120-2 Acceleration settings. These are also covered in ‘Introduction to CNC for a Total Novice – Setting up a laser’. I will duplicate those here as they apply to using a spindle as well.
- $110-2 Maximum feed rate.
- $30 and $31 Spindle RPM.

- $130-2 Maximum travel settings along with homing and soft limits are covered a bit superficially. I have a standard 3018-PRO without limit switches so they do not apply to my router.

WARNING: All my observations are based on Grbl 1.1.f. There are many possible configuration options which your board manufacturer or distributor could have changed. All observations are taken using a Woodpecker CamxTool 3.4 router motherboard from SainSmart on m unmodified SainSmart Genimitsu 3018-PRO. Using either LaserGRBL (with a SainSmart 5.5W Laser Module) or Candle as appropriate on my PC. Although the methods I used to determine what setting changes mean are probably applicable to all Grbl routers and Laser Cutters. This gives a very low sample size, in fact a sample size of ONE, so please do not accept any figures or other results blindly.

I am producing this as a document, mainly because It is an edited series of notes I made, partly because I am tired of watching instructional videos on YouTube which play at Mach 2 and so I am constantly stopping, rewinding and re-watching. Also I have been told I have a body made for Radio, a voice most suited to the Deaf and I still haven’t worked out how to use the video camera on my phone properly.

### Disclaimer

Yeah nowadays it has to be included, and it makes sense as I accept NO liability for anything I may say, write or think.

1. I am a total novice (or was when I started out). I MAKE NO CLAIM THAT ANYTHING I SAY IS CORRECT! All this is based on searching the Internet, forum comments.... and my own experiences.
2. This is based solely on the one I have, if there are variations or different versions out there I have not seen them.
3. If you have and are using a Laser module, even the lowest powered is powerful enough to destroy your vision completely, and that of any pets, children, spectators etc. SO EXCLUDE THEM AND USE THE GOGGLES!
4. These are power tools, sharp pieces of metal designed to cut things while rotating at high speed and throwing small bits away also at high speed. Keep everybody’s fingers out! A wood chip flying up your nose is nothing to be sneezed at, never mind in one of your eyes.
5. Take account of the materials you are using and take adequate precautions, dust and ashes can be harmful.
6. I work in mm. Why anyone still uses inches for design work is a mystery. But then I still think of temperatures in Fahrenheit, anything beyond 100m in miles and property plot sizes in acres!
7. I have been told by lots of people that my sense of humour is at the least a bit strange. I do not apologise for it.

Any corrections, clarifications or discussion welcome. You can find me on the Facebook SainSmart
Genmitsu CNC Routers Group as Graham Bland. https://www.facebook.com/groups/SainSmart.GenmitsuCNC/

### Accompanying files

NOTE: Facebook has a problem, it will not allow compressed (.zip, .gz, ......) to be uploaded to the Files section of any group, but it bases this decision solely on the file extension, not the contents.

It is easy to bypass this by changing the file extension before uploading, I use .zip files, and rename them to .zipp This means that after downloading you will have to reverse this by renaming any xx.zipp file to xx.zip, windows will issue warnings that you are probably going to make the file unusable, just ignore it and rename anyway. Then you can open and extract the files as you wish.

So you there may be 2 versions in the files section. One an xx.pdf which is just this document, and if there are any accompanying files with it an xx.zipp with the .pdf and everything else.

Accompanying files for this section are:

TracingTest GCode-V2.xlsx | Excel spreadsheet which generates simple GCode used for testing the settings, mainly the acceleration test is relevant here.
AccelTest.nc | Sample GCode file for the acceleration tests
1sainsmart.nc | Sample GCode file to engrave ‘sainsmart’ used with a max spindle speed of 1000
1sainsmart8000.nc | Sample GCode file to engrave ‘sainsmart’ modified for a max spindle speed of 8000
dragon.nc | Sample GCode file of a dragon engraving with a max spindle speed of 1000. (NOTE: pretty but takes 3+ hours to complete)
Dragon8000.nc | Sample GCode file of a dragon engraving with a max spindle speed of 8000

## Viewing and changing your settings

Load Candle (other software is available, I mainly use Candle) on your PC and connect to your router.

Locate the Console Command box and send $$ to the router, this will return a series of $x=y lines where x is the parameter number and y is the current value.

To change a setting send a command of $x=y to the router, this will change the setting and store it until you specifically change it again. For example to turn Laser Mode off send $32=0.

### Saving your settings

In the words of a man who some would call wise (Only on a dark foggy night never having met him before and without the benefit of hindsight)

## Before you start a journey first put a cross on the map marking where you set out from. That way returning home will be much easier!

### Me -Just now!

Seriously though before you start to make changes, save your settings! Send a $$ command and it will return them all. Copy and paste them into a text editor and save the file as ‘BeforeIScrewedEverythingUp.txt’ or something similar so that you can easily go back to the starting position if needed.

## $120-2 Acceleration settings

From the Grbl Configuration guide:
$120, $121, $122 – [X,Y,Z] Acceleration, mm/sec^2
This sets the axes acceleration parameters in mm/second/second. Simplistically, a lower value makes Grbl ease slower into motion, while a higher value yields tighter moves and reaches the desired feed rates much quicker. Much like the max rate setting, each axis has its own acceleration value and are independent of each other. This means that a multi-axis motion will only accelerate as quickly as the lowest contributing axis can.
Again, like the max rate setting, the simplest way to determine the values for this setting is to individually test each axis with slowly increasing values until the motor stalls. Then finalize your acceleration setting with a value 10-20% below this absolute max value. This should account for wear, friction, and mass inertia. We highly recommend that you dry test some G-code programs with your new settings before committing to them. Sometimes the loading on your machine is different when moving in all axes together.

My default Value was 30 mm/sec/sec often expressed as mm/sec²
, they both mean the same.

If you imagine cutting a straight line starting from rest Grbl uses the acceleration values to control the increase in speed of the spindle up to the desired feed rate and to slow down towards the end of the line.

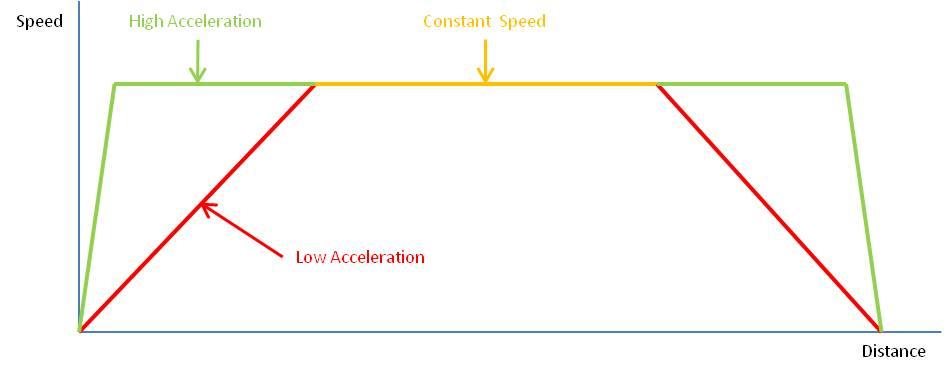
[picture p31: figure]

So:

Time taken, in seconds, to achieve full feed rate starting from zero
Feed Rate | Acceleration (mm/sec/sec)
(mm/min) | (mm/sec) | 30 | 50 | 100 | 500 | 1,000 | 5,000 | 10,000 | 100,000
1000 | 16.67 | 0.556 | 0.333 | 0.167 | 0.033 | 0.017 | 0.003 | 0.002 | 0.000
750 | 12.50 | 0.417 | 0.250 | 0.125 | 0.025 | 0.013 | 0.003 | 0.001 | 0.000
500 | 8.33 | 0.278 | 0.167 | 0.083 | 0.017 | 0.008 | 0.002 | 0.001 | 0.000
250 | 4.17 | 0.139 | 0.083 | 0.042 | 0.008 | 0.004 | 0.001 | 0.000 | 0.000
75 | 1.25 | 0.042 | 0.025 | 0.013 | 0.003 | 0.001 | 0.000 | 0.000 | 0.000

This table shows the effect of acceleration values on the time for the router to get up to speed depending on the feed rate assuming the spindle or laser is at rest to start with. So if you start a line from rest at a feed rate of 1000 with an acceleration of 30mm/sec

2
it will take over ½ a second before it is at full speed. No wonder the burn when using a laser is heavier!

I do apologise that most of the examples used are with a Laser. That is just because if you are using a bit in a spindle the only benefit you will see is decreased times to perform a job. With a laser the effects are just more obvious. Grbl does include compensation for the laser over burning as it accelerates when Laser mode is set, but IMHO it doesn’t work very well.

These settings ONLY determine the acceleration of the spindle along the axes, letting the spindle reach its specified rotational speed is totally separate. Consider making an ‘air cut’ for a few mm before encountering the stock, the spindle would already be rotating at full speed and moving at the specified speed before encountering the stock – no problem there.

Remember the board could be trying to move a big spindle motor, for bigger machines maybe 5Hp rather than the little one we have and 5 horses weigh a lot, also a much bigger and heavier bed, larger stock....! I must admit that if I was responsible for the default values I would be very conservative as well.

Unless you are only moving the spindle along in a single axis at a time the acceleration values on all the axes it is moving in will affect each other. Imagine a 45˚ movement on X and Y, the spindle can only be accelerated as the lower of the X and Y accelerations to keep the line straight. So I need to find hopefully a common value which works for all of them.

I started by setting the X axis acceleration from the default of 30 mm/Sec²
to 50. The instructions say to listen for the stepper motor stalling when it is being asked to do too much work. Well apart from possibly an initial click, which I surmised came from the anti backlash nut moving slightly, no problem.

Well to cut a long story short I rapidly reached an acceleration value of 100,000mm/Sec²
on the X
axis without any visible or audible evidence of stalling the stepper motor (with the SainSmart 5.5W laser fitted). TOO EASY! All things that are too easy are wrong 99.99% of the time! Perhaps the stepper motors stalling under acceleration is not easily determined by eye or ear? And why a default value of 30 should be set if a possible correct value could be 100,000! (But then I remembered this is a small machine and default settings should always be conservative)

So back to the TracingTest Gcode generator spreadsheet. I thought I would engrave a series of shapes like this:

20mm square by default, it mixes horizontal, vertical, diagonal and circle movements, G0 (rapid non cutting movements) and G1 (cutting movements) so it should be fairly easy to see if the stepper motors are stalling and missing steps by the lines becoming misaligned.

NOTE: The circle is only approximately aligned with the lines, nowadays even thinking about trigonometry tends to drive me to drink! So let the intersection of the diagonals AC and BD define the midpoint of the circle.......

A series of these cannot be cut in a single .nc file as Grbl objects (quite rightly) to changing parameters such as $120 in the middle of a GCode file. So the file ‘LaserAccelerationTest-xxx.nc’ produced from the spreadsheet just sets the acceleration ($120-122) values to xxx and draws a single shape, then positions the laser ready to start another one to its right.

.nc files are also provided for testing with a spindle motor and an engraving or V bit, these are SpindleAccelerationTest-xxx.nc

If you want your own values in the .nc file for your own tests either edit one of the .nc files to change the $120-122 lines between each box or delete these lines completely and change the settings before each run manually using console commands. Using the spreadsheet is easier but you have to have MS Excel.

So:

- Set the WCS origin position.
- Run the program.
- Load the next .nc file with higher acceleration values.
- Repeat.

The WCS origin for this is the bottom left. Any missed steps will be cumulative and should be easily visible (well not 1 or 2 steps but you know what I mean).

I ran a set of samples using a 5.5W Laser at varying accelerations, this will only test the X and Y axes but that should be a good start. To stress things further I ran the tests with a 3.15kg weight (OK it was a wine box but it was not harmed during this experiment) on the bed. As far as acceleration goes this should put a greater strain on the Y axis.

These are the results: From top left the acceleration values are 30,60,120,200,500 then on the second row 750, 1,000 5,000 10,000 and 100,000.

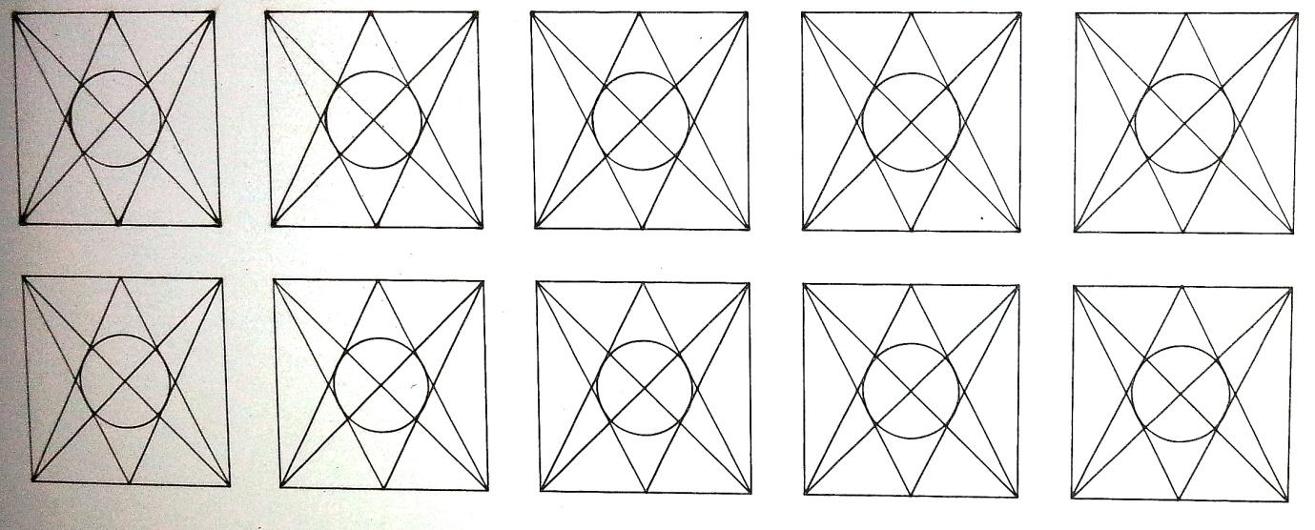
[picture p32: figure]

The tests were run using a piece of 3mm card (I didn’t want it to burn through). I expected this to show up deviations first on the Y axis by trying to accelerate the mass.

Examining this (and please excuse the photography), at my default of 30 mm/sec²
all of the vertices
are over-burnt, including the circle (which starts cutting on its middle left). At an acceleration of 500 mm/sec²

(top right) all of this has largely disappeared and the cut is much cleaner. 5,000 mm/sec² sees the last vestiges of a thicker line on the left of the circle disappear, From then on no real discernible difference for this test, and I am looking at the original, not the photo!

But no misalignment of the lines which means no missed steps!

A very pleasant side effect is that the job time went from 32 seconds with the acceleration set at 30 mm/sec²

to 21 seconds at 5000 mm/sec² .

Not at first really believing these results I decided to run my boxes test, at 3 acceleration settings-30(default) 500 and 100,000 mm/sec/sec. (File is LaserDrawBoxes.nc The acceleration values have to be set manually before each run)

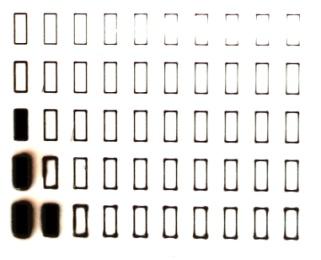
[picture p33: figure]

At 500 mm/sec²

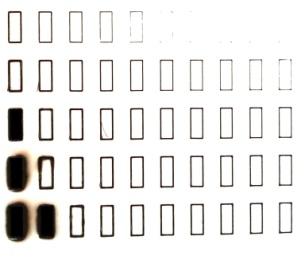
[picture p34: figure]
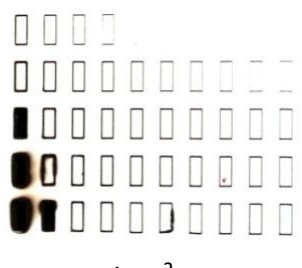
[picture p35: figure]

there are still some faint dots at the marginal corners, at 100,000 mm/sec² these
have all disappeared. No missed steps!

I have now set my $120-122 values to 5,000 mm/sec² .

## $110-2 Maximum feed rate

From the Grbl Configuration guide:
$110, $111 and $112 – [X,Y,Z] Max rate, mm/min
This sets the maximum rate each axis can move. Whenever Grbl plans a move, it checks whether or not the move causes any one of these individual axes to exceed their max rate. If so, it'll slow down the motion to ensure none of the axes exceed their max rate limits. This means that each axis has its own independent speed, which is extremely useful for limiting the typically slower Z-axis.
The simplest way to determine these values is to test each axis one at a time by slowly increasing max rate settings and moving it. For example, to test the X-axis, send Grbl something like G0 X50 with enough travel distance so that the axis accelerates to its max speed. You'll know you've hit the max rate threshold when your steppers stall. It'll make a bit of noise, but shouldn't hurt your motors. Enter a setting a 10-20% below this value, so you can account for wear, friction, and the mass of your workpiece/tool. Then, repeat for your other axes.
NOTE: This max rate setting also sets the G0 seek rates.

My default Values were $110=1000, $111=1000, $112=800 mm/min.

### Why does the Z axis have a lower default value?

Well the documentation says it is ‘typically slower’ But on a 3018-PRO it has the same pitch on the threaded rod and the same stepper motor and motor driver so I don’t think this applies to the 3018-PRO.

The Z axis movement speed would typically match up to the Plunge rate, the rate the bit heads straight down into the stock. Too fast would be – well Bad!

But remember these are Maximum rates; they won’t make the slightest bit of difference unless your GCode specifies a feed rate greater than the maximum, in that case the maximum feed rate will be used instead.

- Max feed rate is 1000, GCode feed rate is 600, 600 is used.

- Max feed rate is 1000, GCode feed rate is 2000, 1000 is used.

Well there is a bit of a difference, they also act as the default G0 (non cutting move) movement rate! But that shouldn’t make a difference!

### A very simple Feed rate test

The Maximum Feed rate is how fast the router can be told to move one or more axes without the motor missing steps. So here is a method to find out what this is.

- Open Candle and connect to the router.
- Set the $110-2 values to something high, 3000 should be plenty, by sending $110=3000 $111=........ as separate commands to the router. If you don’t do this the existing max federate settings will override any higher values rendering this test useless!
- Position the spindle somewhere towards the middle on all axes.
- Set the Jog Step to 10mm, other values are fine and work but 10mm is enough.
- Set the Jog feed rate to the value to test, I suggest starting at 1500 and going up in 100’s to start with.
- Now Jog left then right (or right then left, it doesn’t matter) and see what happens.
- If everything works fine, no funny noises and more importantly the spindle moves as expected, increase the feed rate and try again.
- Eventually as the feed rate gets larger you will hear the stepper motor make a squeaky noise and the axis will not move properly. You have now exceeded the feed rate on the axis!
- Make a note of the number or try different feed rates between the last value that worked and the one that failed. Then make a note of the highest number that worked with the axis you were testing.
- NOTE: Often going back to the previously good value may fail the first time, I think this is down to Grbl or Candle though so try it a few times and make a judgement.
- We are not trying to be exact here as when this process is finished we are going to apply a margin for safety so it’s not really important if it’s 2249 or 2251.
- Repeat for the Y and Z axes.

You should now have 3 values, one for each axis, which is the highest number it worked at reliably.

These values should be pretty much the same, if they are significantly out you may have a problem with an axis binding somewhere.

These are the values I ended up with; I used final steps of 50:

X | 2100
Y | 2200
Z | 2150
To determine the maximum Feed rate to use:
- Take the Lowest value
- Multiply it by 0.8 to reduce it by 20% for safety.
- Round it to a convenient number, I don’t really want to set the values to 2014.95, 2000 will do.

This is your new maximum federate value, set this by sending $110=yyyy then $111=yyyy then $112=yyyy to your router.

Now as a final test jog the spindle around to the (near) limits of travel on all the axes, there should be no problems at all.

I have now set my $110-112 values to 1600 mm/min.

## $30 and $31 Spindle RPM

From the Grbl Configuration guide:
$30 - Max spindle speed, RPM
This sets the spindle speed for the maximum 5V PWM pin output. For example, if you want to set 10000rpm at 5V, program $30=10000. For 255rpm at 5V, program $30=255. If a program tries to set a higher spindle RPM greater than the $30 max spindle speed, Grbl will just output the max 5V, since it can't go any faster. By default, Grbl linearly relates the max-min RPMs to 5V-0.02V PWM pin output in 255 equally spaced increments. When the PWM pin reads 0V, this indicates spindle disabled. Note that there are additional configuration options are available in config.h to tweak how this operates. $31 - Min spindle speed, RPM
This sets the spindle speed for the minimum 0.02V PWM pin output (0V is disabled). Lower RPM values are accepted by Grbl but the PWM output will not go below 0.02V, except when RPM is zero. If zero, the spindle is disabled and PWM output is 0V.

NOTE: The 0.02V and 5V referred to here is the output of the Arduino processor which works at 0-5V, on the router motherboard this is then fed into an ‘amplifier’ which converts into the 0-24V fed to the spindle motor. Just mentioning it.

My default Values are $30=1000, $31=0 RPM.
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

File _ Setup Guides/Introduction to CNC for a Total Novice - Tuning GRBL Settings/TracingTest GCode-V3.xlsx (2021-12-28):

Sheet: Draw Lines
TracingTest Gcode Generator-V3
 | Draw 10 vertical Lines with Laser |  |  | Purpose
 | PARAMETERS | NOTE: PARAMETER VALUES ARE NOT CHECKED |  | To draw lines on the stock at varying speed and feed to determine what works best.
 | Power Start | 200 | Power for line 1 (1-1,000) | Instructions
 | Power Step | 33.3 |  | Set the line height and spacing as required.
 | Power End | 500 | Power for line 10 (1-1,000) | Set the laser power start and end, for each each line the power will be adjusted by the calculated power step.
 | Feed Start (mm/Min) | 300 | Feed for line 1 (1-1,000) | To keep a constant power for all lines set the start equal to the end.
 | Feed Step (mm/Min) | 0.0 |  | Set the feed rate start and end, adjusted the same as the power.
 | Feed End (mm/Min) | 300 | Feed for line 10 (1-1,000) | Select and copy the Gcode, just the green box, into a text editor such as notepad and save as a .nc file
 | Line Height(mm) | 10 |  | Before running the file check the Laser Focus, position the laser to the start and zero all the axes.
 | Line Spacing(mm) | 2 |  | The laser will return to the WCS origin after drawing the last line
 |  | Gcode | Meaning
 |  | $32=1 | Set Laser Mode On, if it's already set dont copy this
 |  | (TracingTest Gcode Generator-V3)
 |  | (Draw 10 vertical Lines with Laser)
 |  | (Power 200/33/500)
 |  | (Feed 300/0/300 mm/Min)
 |  | (Line Height 10, Spacing 2 mm)
 |  | G94 | Feed rate is units/minute
 |  | G17 | Select XY plane
 |  | G21 | Interpret all distances in mm
 |  | G90 | Set Absolute coordinate mode
 |  | G0 X0 Y0 | Go to the home (WCS) position.
 |  | G91 | Set Relative coordinate mode
 |  | M3 | Turn the laser on
 |  | (Draw lines)
 |  | G1 Y10 F300 S200 | Burn up
 |  | G0 X2 Y-10 | Position rapidly to the start of the next line
 |  | G1 Y10 F300 S233
 |  | G0 X2 Y-10
 |  | G1 Y10 F300 S266
 |  | G0 X2 Y-10
 |  | G1 Y10 F300 S300
 |  | G0 X2 Y-10
 |  | G1 Y10 F300 S333
 |  | G0 X2 Y-10
 |  | G1 Y10 F300 S366
 |  | G0 X2 Y-10
 |  | G1 Y10 F300 S400
 |  | G0 X2 Y-10
 |  | G1 Y10 F300 S433
 |  | G0 X2 Y-10
 |  | G1 Y10 F300 S466
 |  | G0 X2 Y-10
 |  | G1 Y10 F300 S500
 |  | G90
 |  | G0 X0 Y0 | Go to to home position, set Absolute Coordinate mode
 |  | M2 | Program end, laser off
 |  | (END OF PROGRAM)

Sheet: Draw Boxes
TracingTest Gcode Generator-V3
 | Laser engrave 10x1-5 Boxes |  |  | Purpose
 | PARAMETERS | NOTE: PARAMETER VALUES ARE NOT CHECKED |  | To draw boxes on the stock at varying speed and feed to determine what works best. Power is varied for each row.
 | Power Start | 150 | Power for row 1 (1-1,000) Adjusted for each row | Feed rate is varied for each column. Number of rows is variable from 1 to 5.
 | Power Step | 150.0 | 1-5 columns of boxes | Instructions
 | Power End | 750 | Power for row x (1-1,000) Adjusted for each row | Set the box height, width and spacing as required.
 | Feed Start (mm/Min) | 100 | Feed Rate for box 1 (1-1,000) Adjusted for each column | Set the laser power start and end, for each each row the power will be adjusted by the calculated power step.
 | Feed Step (mm/Min) | 100.0 | 10 boxes per row | If only one row is selected - it won't change. To keep a constant power for all rows set the start equal to the end.
 | Feed End (mm/Min) | 1000 | Feed Rate for box 10 (1-1,000) Adjusted for each column | Set the feed rate start and end, adjusted for each column.
 | Box Height(mm) | 5 |  | Select and copy the Gcode, just the green box, into a text editor such as notepad and save as a .nc file
 | Box Width (mm) | 2 |  | Before running the file check the Laser Focus, position the laser to the start and zero all the axes.
 | Box Spacing (mm) | 3 |  | The laser will return to the WCS origin after drawing the last row of boxes.
 | Box Rows | 5 | 1 to 5
 |  | Gcode | Meaning
 |  | $32=1 | Set Laser Mode On, if it's already set dont copy this
 |  | (TracingTest Gcode Generator-V3) | Comment
 |  | (Laser engrave 10x1-5 Boxes) | Comment
 |  | (Power-Row 150/150/750) | Comment
 |  | (Feed-Col 100/100/1000 mm/Min) | Comment
 |  | (Box Height 5, Width 2, Spacing 3 mm. Rows 5) | Comment
 |  | G94 | Feed rate is units/minute
 |  | G17 | Select XY plane
 |  | G21 | Interpret all distances in mm
 |  | G90 | Set Absolute coordinate mode
 |  | G0 X0 Y32 | Go to the start position. (WCS origin is bottom left)
 |  | G91 | Set Relative coordinate mode
 |  | M3 | Turn the laser on
 |  | (Draw 10 boxes in a row varying Feed) | Comment
 |  | S150 | Set Speed for this Row
 |  | G1 Y5 F100 | Burn up setting Feedrate for box
 |  | G1 X2 | Right
 |  | G1 Y-5 | Down
 |  | G1 X-2 | Left
 |  | G0 X5 | Position rapidly to the start of the next box
 |  | G1 Y5 F200 | Burn up setting Feedrate for box
 |  | G1 X2 | Right
 |  | G1 Y-5 | Down
 |  | G1 X-2 | Left
 |  | G0 X5 | Position rapidly to the start of the next box
 |  | G1 Y5 F300 | Burn up setting Feedrate for box
 |  | G1 X2 | Right
 |  | G1 Y-5 | Down
 |  | G1 X-2 | Left
 |  | G0 X5 | Position rapidly to the start of the next box
 |  | G1 Y5 F400 | Burn up setting Feedrate for box
 |  | G1 X2 | Right
 |  | G1 Y-5 | Down
 |  | G1 X-2 | Left
 |  | G0 X5 | Position rapidly to the start of the next box
 |  | G1 Y5 F500 | Burn up setting Feedrate for box
 |  | G1 X2 | Right
 |  | G1 Y-5 | Down
 |  | G1 X-2 | Left
 |  | G0 X5 | Position rapidly to the start of the next box
 |  | G1 Y5 F600 | Burn up setting Feedrate for box
 |  | G1 X2 | Right
 |  | G1 Y-5 | Down
 |  | G1 X-2 | Left
 |  | G0 X5 | Position rapidly to the start of the next box
 |  | G1 Y5 F700 | Burn up setting Feedrate for box
 |  | G1 X2 | Right
 |  | G1 Y-5 | Down
 |  | G1 X-2 | Left
 |  | G0 X5 | Position rapidly to the start of the next box
 |  | G1 Y5 F800 | Burn up setting Feedrate for box
 |  | G1 X2 | Right
 |  | G1 Y-5 | Down
 |  | G1 X-2 | Left
 |  | G0 X5 | Position rapidly to the start of the next box
 |  | G1 Y5 F900 | Burn up setting Feedrate for box
 |  | G1 X2 | Right
 |  | G1 Y-5 | Down
 |  | G1 X-2 | Left
 |  | G0 X5 | Position rapidly to the start of the next box
 |  | G1 Y5 F1000 | Burn up setting Feedrate for box
 |  | G1 X2 | Right
 |  | G1 Y-5 | Down
 |  | G1 X-2 | Left
 |  | G0 X-45 Y-8 | Position to start of the next row or WCS home at end
 |  | (Start Next Row)
 |  | S300
 |  | G1 Y5 F100
 |  | G1 X2
 |  | G1 Y-5
 |  | G1 X-2
 |  | G0 X5
 |  | G1 Y5 F200
 |  | G1 X2
 |  | G1 Y-5
 |  | G1 X-2
 |  | G0 X5
 |  | G1 Y5 F300
 |  | G1 X2
 |  | G1 Y-5
 |  | G1 X-2
 |  | G0 X5
 |  | G1 Y5 F400
 |  | G1 X2
 |  | G1 Y-5
 |  | G1 X-2
 |  | G0 X5
 |  | G1 Y5 F500
 |  | G1 X2
 |  | G1 Y-5
 |  | G1 X-2
 |  | G0 X5
 |  | G1 Y5 F600
 |  | G1 X2
 |  | G1 Y-5
 |  | G1 X-2
 |  | G0 X5
 |  | G1 Y5 F700
 |  | G1 X2
 |  | G1 Y-5
 |  | G1 X-2
 |  | G0 X5
 |  | G1 Y5 F800
 |  | G1 X2
 |  | G1 Y-5
 |  | G1 X-2
 |  | G0 X5
 |  | G1 Y5 F900
 |  | G1 X2
 |  | G1 Y-5
 |  | G1 X-2
 |  | G0 X5
 |  | G1 Y5 F1000
 |  | G1 X2
 |  | G1 Y-5
 |  | G1 X-2
 |  | G0 X-45 Y-8
 |  | (Start Next Row)
 |  | S450
 |  | G1 Y5 F100
 |  | G1 X2
 |  | G1 Y-5
 |  | G1 X-2
 |  | G0 X5
 |  | G1 Y5 F200
 |  | G1 X2
 |  | G1 Y-5
 |  | G1 X-2
 |  | G0 X5
 |  | G1 Y5 F300
 |  | G1 X2
 |  | G1 Y-5
 |  | G1 X-2
 |  | G0 X5
 |  | G1 Y5 F400
 |  | G1 X2
 |  | G1 Y-5
 |  | G1 X-2
 |  | G0 X5
 |  | G1 Y5 F500
 |  | G1 X2
 |  | G1 Y-5
 |  | G1 X-2
 |  | G0 X5
 |  | G1 Y5 F600
 |  | G1 X2
 |  | G1 Y-5
 |  | G1 X-2
 |  | G0 X5
 |  | G1 Y5 F700
 |  | G1 X2
 |  | G1 Y-5
 |  | G1 X-2
 |  | G0 X5
 |  | G1 Y5 F800
 |  | G1 X2
 |  | G1 Y-5
 |  | G1 X-2
 |  | G0 X5
 |  | G1 Y5 F900
 |  | G1 X2
 |  | G1 Y-5
 |  | G1 X-2
 |  | G0 X5
 |  | G1 Y5 F1000
 |  | G1 X2
 |  | G1 Y-5
 |  | G1 X-2
 |  | G0 X-45 Y-8
 |  | (Start Next Row)
 |  | S600
 |  | G1 Y5 F100
 |  | G1 X2
 |  | G1 Y-5
 |  | G1 X-2
 |  | G0 X5
 |  | G1 Y5 F200
 |  | G1 X2
 |  | G1 Y-5
 |  | G1 X-2
 |  | G0 X5
 |  | G1 Y5 F300
 |  | G1 X2
 |  | G1 Y-5
 |  | G1 X-2
 |  | G0 X5
 |  | G1 Y5 F400
 |  | G1 X2
 |  | G1 Y-5
 |  | G1 X-2
 |  | G0 X5
 |  | G1 Y5 F500
 |  | G1 X2
 |  | G1 Y-5
 |  | G1 X-2
 |  | G0 X5
 |  | G1 Y5 F600
 |  | G1 X2
 |  | G1 Y-5
 |  | G1 X-2
 |  | G0 X5
 |  | G1 Y5 F700
 |  | G1 X2
 |  | G1 Y-5
 |  | G1 X-2
 |  | G0 X5
 |  | G1 Y5 F800
 |  | G1 X2
 |  | G1 Y-5
 |  | G1 X-2
 |  | G0 X5
 |  | G1 Y5 F900
 |  | G1 X2
 |  | G1 Y-5
 |  | G1 X-2
 |  | G0 X5
 |  | G1 Y5 F1000
 |  | G1 X2
 |  | G1 Y-5
 |  | G1 X-2
 |  | G0 X-45 Y-8
 |  | (Start Next Row)
 |  | S750
 |  | G1 Y5 F100
 |  | G1 X2
 |  | G1 Y-5
 |  | G1 X-2
 |  | G0 X5
 |  | G1 Y5 F200
 |  | G1 X2
 |  | G1 Y-5
 |  | G1 X-2
 |  | G0 X5
 |  | G1 Y5 F300
 |  | G1 X2
 |  | G1 Y-5
 |  | G1 X-2
 |  | G0 X5
 |  | G1 Y5 F400
 |  | G1 X2
 |  | G1 Y-5
 |  | G1 X-2
 |  | G0 X5
 |  | G1 Y5 F500
 |  | G1 X2
 |  | G1 Y-5
 |  | G1 X-2
 |  | G0 X5
 |  | G1 Y5 F600
 |  | G1 X2
 |  | G1 Y-5
 |  | G1 X-2
 |  | G0 X5
 |  | G1 Y5 F700
 |  | G1 X2
 |  | G1 Y-5
 |  | G1 X-2
 |  | G0 X5
 |  | G1 Y5 F800
 |  | G1 X2
 |  | G1 Y-5
 |  | G1 X-2
 |  | G0 X5
 |  | G1 Y5 F900
 |  | G1 X2
 |  | G1 Y-5
 |  | G1 X-2
 |  | G0 X5
 |  | G1 Y5 F1000
 |  | G1 X2
 |  | G1 Y-5
 |  | G1 X-2
 |  | G0 G90 X0 Y0
 |  | M2
 |  | (END OF PROGRAM)
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

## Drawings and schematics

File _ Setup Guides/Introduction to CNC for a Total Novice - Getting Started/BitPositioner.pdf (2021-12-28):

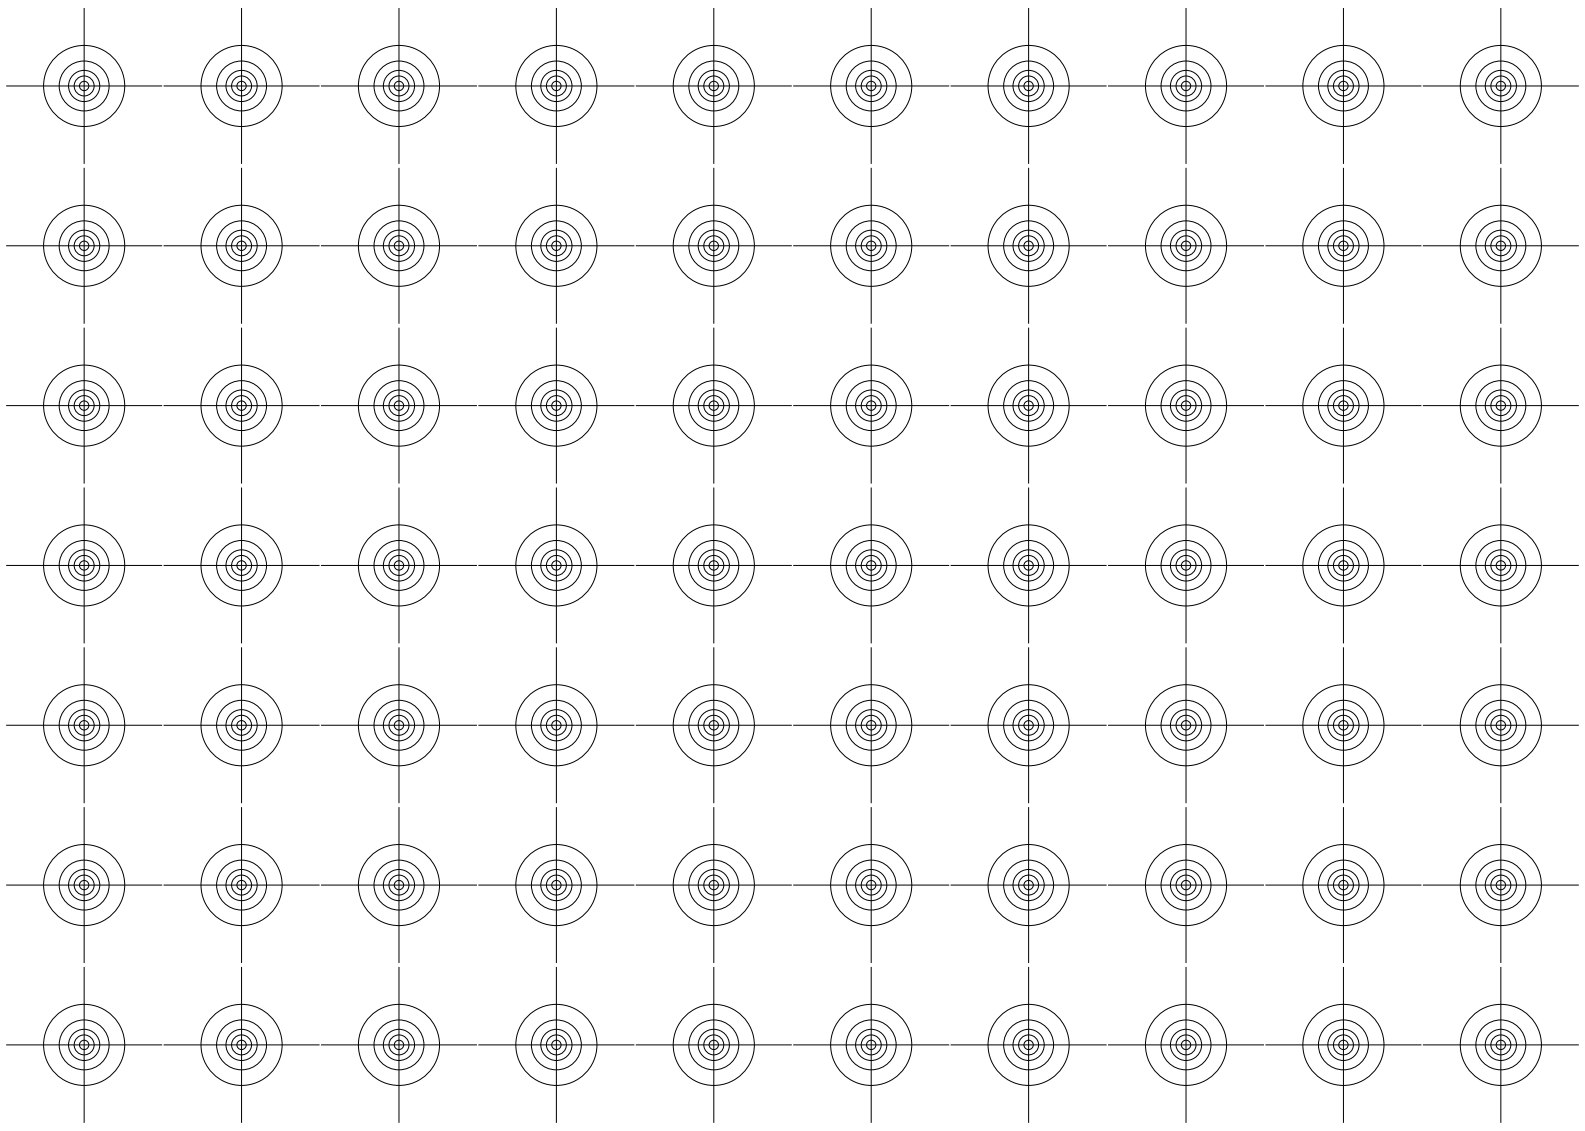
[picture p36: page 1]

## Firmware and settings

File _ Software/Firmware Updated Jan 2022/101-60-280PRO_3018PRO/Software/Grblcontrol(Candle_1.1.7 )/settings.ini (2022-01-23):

[General]
port=COM11
baud=115200
toolDiameter=3
toolLength=30
antialiasing=true
msaa=true
vsync=false
zBuffer=false
simplify=false
simplifyPrecision=1
jogStep=10
spindleSpeed=500
lineWidth=1.5
arcLength=0
arcDegree=5
arcDegreeMode=true
showProgramCommands=false
showUICommands=true
spindleSpeedMin=0
spindleSpeedMax=1000
moveOnRestore=false
restoreMode=0
rapidSpeed=2500
heightmapProbingFeed=10
acceleration=100
toolAngle=15
toolType=1
fps=60
queryStateTime=40
autoScroll=false
header=@ByteArray(\0\0\0\xff\0\0\0\0\0\0\0\x1\0\0\0\x1\0\0\0\0\0\0\0\0\0\0\0\0\0\0\0\0\x6\x30\0\0\0\x2\0\0\0\x4\0\0\0}\0\0\0\x5\0\0\0}\0\0\x2\xa3\0\0\0\x6\0\x1\0\0\0\0\0\0\x1\0\0\0\0\0\0\0}\0\0\0\x32\0\0\0\x84\0\0\0\0\0\0\0\x6\0\0\0\x63\0\0\0\x1\0\0\0\0\0\0\x1\x5\0\0\0\x1\0\0\0\0\0\0\0\x9b\0\0\0\x1\0\0\0\0\0\0\0\xa0\0\0\0\x1\0\0\0\x1\0\0\0\0\0\0\0\x1\0\0\0\0\0\0\0\0\0\0\0\x1\0\0\0\0\0\0\x3\xe8\0)
splitter=@ByteArray(\0\0\0\xff\0\0\0\x1\0\0\0\x2\0\0\x1\xd0\0\0\x1\x39\x1\0\0\0\f\x1\0\0\0\x2\0)
formGeometry=@ByteArray(\x1\xd9\xd0\xcb\0\x2\0\0\0\0\x1:\0\0\0>\0\0\x4\xf7\0\0\x3\xa0\0\0\x1\x43\0\0\0\x62\0\0\x4\xee\0\0\x3\x97\0\0\0\0\0\0\0\0\a\x80)
formSettingsSize=@Size(705 509)
feedOverride=false
feed=500
heightmapPanel=false
spindlePanel=true
feedPanel=true
jogPanel=true
keyboardControl=false
autoCompletion=true
units=0
storedX=0
storedY=0
storedZ=0
recentFiles=D:/Users/Administrator/Desktop/haiyun.nc, D:/Users/Administrator/Desktop/CNNNNNNNNNC/nc/haiyun.nc, D:/Users/Administrator/Desktop/piglet2.nc, D:/Users/Administrator/Desktop/Untitled.nc, N:/Test code/sainlogo.nc
recentHeightmaps=@Invalid()
touchCommand="G21G91G38.2Z-30F100; G0Z1; G38.2Z-2F10"
safePositionCommand="G21G90; G53G0Z0"
panelHeightmapVisible=false
panelSpindleVisible=true
panelFeedVisible=true
panelJogVisible=true
fontSize=9
consoleMinHeight=74
heightmapBorderX=-0.25
heightmapBorderY=0
heightmapBorderWidth=13.25
heightmapBorderHeight=19.620000000000001
heightmapBorderShow=true
heightmapGridX=2
heightmapGridY=2
heightmapGridZTop=1
heightmapGridZBottom=-1
heightmapGridShow=true
heightmapInterpolationStepX=20
heightmapInterpolationStepY=20
heightmapInterpolationType=0
heightmapInterpolationShow=true
ToolpathZMovement=#ff0000
ToolpathHighlight=#9182e6
ToolpathStart=#ff0000
ToolpathEnd=#00ff00
VisualizerBackground=#ffffff
VisualizerText=#000000
Tool=#ff9900
ToolpathDrawn=#d9d9d9
ToolpathNormal=#000000
grayscaleSegments=false
grayscaleSCode=true
drawModeVectors=true
laserPowerMin=0
laserPowerMax=255
lastFolder=D:/Users/Administrator/Desktop
recentCommands="S111=1000", "S110=1000", $$, "$112=100", "$111=100", "$110=100", $$, "$102=800", "$101=800", "$100=800"
userCommandsPanel=false
panelUserCommandsVisible=false
userCommands1=G1
userCommands3=G3
userCommands2=G2
userCommands0=G0
ignoreErrors=false
autoLine=true
panelOverridingVisible=false
feedOverrideValue=100
rapidOverride=false
rapidOverrideValue=100
spindleOverride=false
spindleOverrideValue=100
jogFeeds=10, 50, 100, 500, 1000, 2000, , 555
jogFeed=1000
jogSteps=Continuously, 0.01, 0.1, 1, 5, 10, 100, , 0.3

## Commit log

2021-03-18 CNC Stuffs
    [Pseudo_Parallel_A.stl, Pseudo_Parallel_B.stl, Two_Part_Vise_Jaw_A.stl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]
2021-03-22 Create 3.175mm Shank Carbide Ball Nose End Mill CNC Engraving Router bit Set 1-3.175mm - eBay.url
2021-12-31 Create CNC 3018 cut clear acrylic - YouTube.url
2022-01-01 Guide updates
    [CNC3018_OcHolder_NoTools.stl, CNC_3018_Milling_Bits_Holder.stl, SainSmart Master Bit Data V1.0.xlsx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]
2022-01-02 Create Fusion 360 Tutorial – Engraving Acrylic with CAM - YouTube.url
2022-01-02 Create TUTORIAL- Intro to CAD-CAM using Fusion 360 - YouTube.url
